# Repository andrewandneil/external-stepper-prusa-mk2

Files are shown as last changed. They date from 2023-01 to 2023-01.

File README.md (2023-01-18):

# External Stepper Drivers for Prusa MK2 Based Printers
Adds the ability to use external TMC stepper drivers on the Prusa MK2/S/2.5/S (any printer that uses the Mini Rambo).

## Purpose
Since the Mini Rambo that powers the original line of Prusas was released, stepper driver technology has come a long way. Now days, the `A4982`s that are hard soldered onto the board are louder and less accurate than more modern offerings from `Trinamic`.

The mission of this project is to create an open source PCB ~~and Case~~ design to allow the use of standard, off the shelf stepper driver boards to be used with printers such as the `Prusa MK2/S/2.5/S`. This will allow the printer to run quieter and smoother, resulting in a nicer experience whilst printing, as well as a nicer quality of print.

Achived by utilising the handily placed test points on the back of the Mini Rambo, this board is able to 'steal' the data signals intended for the `A4982`s on the board and give them to the user's choice of stepper drivers.

Side note: if you have a blown driver on your Mini Rambo, this is a great way of getting it up and running again. Simiply solder this board to the pads corresponding to the dead driver on the back of the board, and hey presto, a functional printer again!

Upon seeing a certain other design on the internet that did the same thing, but was closed source, I decided to create my own design from scratch, and make it open source! You will find all KiCAD PCB Design files, along with the F3D files and STEP files for the case I have created. 

## Functionality
Tested mostly with the `TMC2208` drivers, however, `TMC2209`s, `TMC2130`s and `TMC2100`s (may require to be in their 'standalone' mode) have all been tested and confirmed to work with this board and the printer. However, do note the graphic towards the bottom left of the PCB for the correct positioning of the jumpers for your stepper drivers.

Compatible with any printer using the Mini Rambo main board, including but not limited to `Prusa i3 MK2`, `Prusa i3 MK2S`, `Prusa i3 MK2.5` and `Prusa i3 MK2.5S`.

## Utilisation
This WILL require modifying your mainboard. However, the modification is not permant and can be reversed at any time. Only requires soldering to 8 fairly large points on the back of the main board. You will also need to get power for the board from somewhere. To do this you have 2 options:
  1. Tap into the 12V supplied from the printer's power supply and run a cable to the socket on the board.
  2. Run either a 12V or 24V external power supply and utilise that. 

The 24V option is your prefered option if you are wanting the drivers to operate as cool and quite as possible, however, please see the [optional](/Guides/PartsList.md/#optional) section of the parts list for more information.

#### Setting Stepper Current
My `TMC2208`s have been set to a Vref voltage of 1V[^1].

## What's Included?
In the repository you will find the KiCAD files if you wish to modify, adapt or improve the board ~~and a 3D printable case for the board, along with a STEP file if you wish to modify, adapat or improve it.~~ (yet to be added).

Please see the [releases](https://github.com/andrewandneil/external-stepper-prusa-mk2/releases) section to find the current Gerber files for the fabrication of the PCB.

## Software Used
  - [KiCAD](https://kicad.org): An amazing, open source, PCB design studio. I encourage you to check it out if you're looking for something like that. Used to design the schematics, PCB and export the Gerber Files.
  - [Fusion 360](https://www.autodesk.com/products/fusion-360): A good all round CAD software, with a free personal license. ~~Used to design the case.~~

## Pictures
To be added

## Cases

### My Case
As of the moment yet to be finalised

### Other People's Cases
In the offchance that someone either, modifies, redesigns, or creates from sctach a new case or related accessory, I'll do my best to add them here.

If you're one of amazing community that might create a case, get in touch with me and I'll link it here, along with any credit due.

## Parts List
Please see [here](/Guides/PartsList.md).

## Assembly Guide
Please see [here](/Guides/AssemblyGuide.md).

## What else
Notice how nowhere in this guide I mentioned the X and Y axis until now? Well, for good reason. If you wanted to you could build a board for the E and Z axis and use it in parallel to a X and Y board (or just use the E and Z board if you're weird like that I suppose). The Z motor plug will need to be split into 2 new plugs (one for ZL and ZR). The board labels the two sockets with X and Y identifiers, but this is more so you can trace which plug goes where. Obvisouly just connect either the X or Y plugs to the E or Z solder pads on the Rambo if you're planning on doing this.

However, logically with the X and Y axis doing the most moving and at the highest speeds, your best bet to make it mostly quiet is just making one for the X and Y.

## Future Plans
I have no clue if I will ever get around to implementing these plans but you might as well know about them (if I don't do them and you're reading this in the future please feel free to 'borrow' these ideas 😉):
  - Creating a board that allows X, Y, E and Z axis drivers all on one board.
  - Creating a 3D printable case for the board.
  - Test the board with even more drivers.
  - Create an easy to follow and detailed guide for assembly.

## Using these Files
This project is protected by a GNU GPL v3.0 license:
  - You are free to use the files and designs to create your own boards in a personal manner[^2].
  - You are also free to use the files and designs to create boards to sell and make a profit, so long as credit is given or a link is added to this GitHub page[^2].
  - You are also free to modify or otherwise change the files and designs included in anyway you see fit, so long as if the project is shared, it follows the GNU GPL v3.0 license and credit is given[^2].

I fully encourage you to do what you see fit with this design, so long as it follows the GNU license[^2]. If you have the know how and have an idea for an improvement, I look forward to see what you can do! After all, that's the spirit of RepRap!

[^2]:**Not legal adivce. Please read [COPYING.txt](/COPYING.txt) for the full GNU GPL v3.0 license**

## Currently Known Issues
##### Will do my best to update if other issues are found
  - Z and E motors will 'squeal' if using TMC drivers on X and Y axis. I believe this to be something to do with microstepping. Only happens if the motors are powered and at a certain rotational degree. *Your quick fix here is to ignore it or make a board for the E and Z axis*
    - It is completely unnoticable during motion. You will only really hear it if your printer is unlucky enough to stop in a rotaional positon where it happens.

## Disclamer
I have tested this board extensively and have yet to run into issues, however, if you choose to do this mod, you do so at your own risk. I, nor any other party involved, offer any kind of warranty with this product. I have done my best to include all relevant information in this GitHub page, to allow you to come to a decision as to wether or not you would like to partake in this mod. This is not a product. You must source and assemble the board yourself. I will do my best to support any issues you may have if I can.

[^1]: My reference voltage and therefore stepper current is just a suggestion not a defintive do it. Do your own research and experimentation to suit your steppers and drivers.

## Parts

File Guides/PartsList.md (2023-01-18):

# Parts You'll Need

### REQUIRED:
  - 1x printer with a functional Mini Rambo.
  - 1x PCB (find the gerber files for production [here](https://github.com/andrewandneil/external-stepper-prusa-mk2/releases/latest)).
  - 1x 2x8 2.54mm Pitch IDC cable.
  - 1x 2x8 2.54mm Pitch IDC PCB through-hole socket.
  - 2x stepper drivers (on breakout boards) of your choice ([see here for a list of working drivers](#your-stepper-driver-options)).
  - 2x Molex SL 1x4 2.54mm Pitch Male Vertical connectors.
    - [For example this from Digikey](https://www.digikey.co.uk/en/products/detail/molex/0705430003/114923).
    - Can be difficult to find these. You can of course suppliment them with standard 1x4 2.54mm pitch male headers if you wish.
  - 1x 2x3 2.54mm Pitch Male header.
  - 4x 1x8 2.54mm Pitch Female headers.
  - 2x 10K 0805 Resistors.
  - 1x wire-to-board terminal block, 5mm pitch with 2 terminals. (you could of course solder the power wires directly to the board if you'd like. Personally I would still use the terminals).
    - Something like:
      - [This from Farnell UK](https://uk.farnell.com/phoenix-contact/mkdsn-1-5-2-5-08-ht-bk/tb-wire-to-brd-2pos-16awg-blk/dp/3241413).
      - [This from Digikey](https://www.digikey.co.uk/en/products/detail/phoenix-contact/1729128/260615?productid=260615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).
      - Or [this on Amazon US](https://www.amazon.com/KeeYees-60pcs-Terminal-Connector-Arduino/dp/B07H5G7GC6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), only the 2 pin terminal type is required.
  - 2x 100uF 25V Radial capacitors, 6.3mm diameter and 2.50mm pitch.
    - Something like: 
      - [This from Farnell UK](https://uk.farnell.com/panasonic/eca1ehg101/cap-100-f-25v-20/dp/9692827).
      - Or [This from Digikey](https://www.digikey.co.uk/en/products/detail/rubycon/25ZL100MEFC6-3X11/3563144).

### Optional:
  - If you want to use an external power supply to power your drivers:
    - **DISCLAIMER: IF YOU CHOOSE THIS ROUTE YOU WILL BE MESSING WITH MAINS VOLTAGE. WETHER YOU BE IN A 110V or 240V COUNTRY THESE VOLTAGES CAN, AND WILL, KILL YOU IF NOT DONE PROPERLY. EITHER GET A QUALIFIED ELECTRICIAN TO HELP YOU OR JUST USE THE PRINTER'S SUPPLY!**
    - Honestly, here is where I am not going to help you with a specific part. 
    - You'll want either a 12V or 24V PSU (I recommend you just go for 24V if you're doing external anyway). 
    - You'll need to know how much current your steppers+drivers are going to use and do a simple `P=I*V` calculation to figure out your wattage. And remember to always OVER estimate your wattage and have headroom!!
    - **Please DO NOT buy a cheap Chinese PSU. Buy something decent if you're doing this, something like a Meanwell**.
  - If you wish to install a fan[^1][^2]:
    - 1x Pin Header, Square Pin, Signal, Wire-to-Board, 2.54 mm, 1 Rows, 3 Contacts, Through Hole Straight.
      - Something like:
        - [This from Farnell UK](https://uk.farnell.com/molex/22-27-2031/connector-header-3pos-1row-2-54mm/dp/9731156).
        - Or [This from Digikey](https://www.digikey.co.uk/en/products/detail/molex/0022232031/26669).
    - 1x Fan.
      - Something like a 40x10mm fan would do nicely for most drivers (a Noctua A4x10 ([Amazon US](https://www.amazon.com/Noctua-Cooling-Blades-Bearing-NF-A4x10/dp/B009NQLT0M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), [Amazon UK](https://www.amazon.co.uk/Noctua-NF-A4x10-Premium-Quiet-40x10mm/dp/B009NQLT0M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)) is perhaps your best option for 12V).

### Tools and Other:
  - Solder.
  - Soldering Iron.
  - Kapton Tape.
  - ~~If adding my 3D Printed case:~~ !(hasn't been finalised yet)!
    - ~~3D Printed case; [found here](https://www.printables.com/social/239130-utterotter/).~~
    - ~~x4 M3x10 Bolts.~~
    - ~~x4 M3 Nuts.~~
    - ~~x2 M3x18 Bolts.~~
  - Various HEX keys for disassembly of the printer.
  - Zip ties to replace cut zip ties during disassembly.
  - Some 20AWG or better guage wire for power delivery.
    - If you choose (and you should) to crimp the ends of these wires:
      - Crimper tool.
      - Crimps.

## Your Stepper Driver Options
Please note these are ones I have tested and worked with my Prusa i3 MK2.5S+.

This board can't magically add sensorless homing to your printer. Any driver that supports this mode will, and can work, but the endstop sensors of the printer are still required.

All drivers must be in their respective standalone modes (i.e. SPI/UART disabled). If you're not sure how to do that for your specific choice of driver Google is your friend.

Make sure your drivers have some form of heatsink included. If not I recommend you buy a fairly large heatsink for the driver.

### IMPORTANT: don't just buy the chip. You need the chip on a breakout board!
   - `Trinamic TMC2208`
     - Must have UART disbaled. (if you're not sure what that is or how to disbale it most `TMC2208` breakout boards have UART disabled by default).
     - One of the easiest and cheapest ways of getting quiet stepper drivers. 
     - Will run moderately hotter than the more modern `TMC2209`.
   - `Trinamic TMC2209`
     - Perhaps the best all round option.
     - Runs the quietest and coolest out of the four options listed here.
     - Sensorless homing does go to waste, along with other driver to board communication functions.
   - `Trinamic TMC2130`
     - Chris Riley has a great [YouTube video](https://www.youtube.com/watch?v=Jh8iwqc1TP0) on how to use the `TMC2130`s in standalone mode. Give it a watch
     - Runs in stealthChop or spreadCycle depending on jumper setup.
   - `Trinamic TMC2100`
     - Perhaps the least relevant option today.
     - Setup is very similar to `TMC2130`.
     - In my test it was the loudest of the four.
     - Runs in stealthChop or spreadCycle depending on jumper setup.

I am sure there are other drivers that are compatible with this setup. Please see [advanced tuning](/Guides/AdvancedTuning.md) if you wish to figure out if your chosen stepper driver is compatible.

[^1]: The fan will run at the voltage you are using for the power input into the board. So if you're running an external 12V power supply or tapping into the power from the printer you will need a 12V fan, or if you're using an external 24V power supply you will need a 24V fan.
[^2]: Fan is not strictly nessecary as if you have large enough heatsinks on your drivers, and don't run the motors at insane current levels, the drivers are perfectly capable of being passively cooled.

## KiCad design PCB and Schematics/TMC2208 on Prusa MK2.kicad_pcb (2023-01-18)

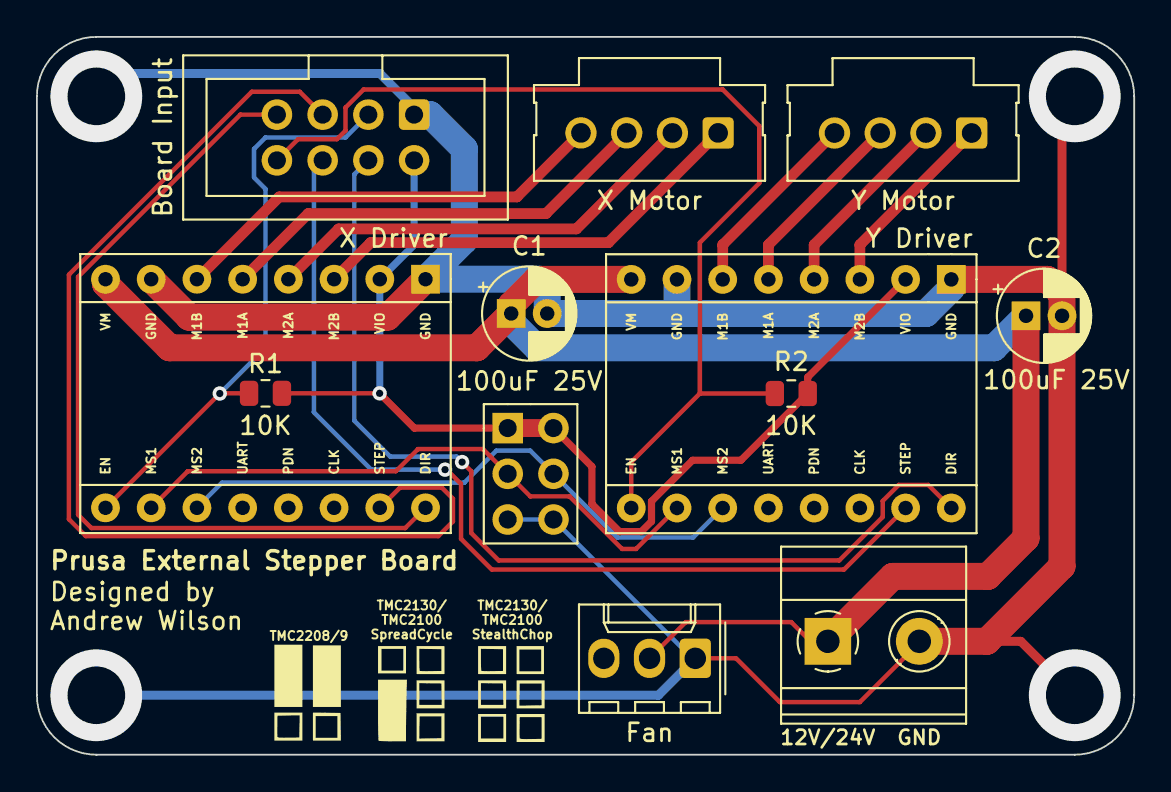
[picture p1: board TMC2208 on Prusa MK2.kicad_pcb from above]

Board: 2 copper layers, 61.0 x 39.9 mm, 12 parts (0 on the bottom side), 19 nets.

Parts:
Board Input: Conn_02x04_Odd_Even; IDC-Header_2x04_P2.54mm_Vertical
C1, C2: 100uF 25V; CP_Radial_D5.0mm_P2.00mm
Fan: Conn_01x03_Male; Molex_KK-254_AE-6410-03A_1x03_P2.54mm_Vertical
J1: Conn_02x03_Counter_Clockwise; PinHeader_2x03_P2.54mm_Vertical
J4: Screw_Terminal_01x02; TerminalBlock_Phoenix_MKDS-1,5-2-5.08_1x02_P5.08mm_Horizont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
R1, R2: 10K; R_0805_2012Metric
X Motor: Conn_01x04_Male; Molex_SL_171971-0004_1x04_P2.54mm_Vertical
XDriver1: Trinamic_Breakout_TMC2208; Trinamic_Breakout-16_15.2x20.3mm
Y Motor: Conn_01x04_Male; Molex_SL_171971-0004_1x04_P2.54mm_Vertical
YDriver1: Trinamic_Breakout_TMC2208; Trinamic_Breakout-16_15.2x20.3mm

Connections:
+12V: C1.1, C2.1, Fan.2, J4.1, XDriver1.8 (VM), YDriver1.8 (VM)
/CONFIG1: J1.3, XDriver1.10 (MS1), YDriver1.10 (MS1)
/CONFIG2: J1.4, XDriver1.11 (MS2), YDriver1.11 (MS2)
GND: Board Input.1, C1.2, C2.2, Fan.1, J1.5, J1.6, J4.2, XDriver1.1 (GND), XDriver1.7 (GND), YDriver1.1 (GND), YDriver1.7 (GND)
unnamed: Board Input.3, R1.1, XDriver1.9 (~ENABLE)
unnamed: Board Input.4, YDriver1.16 (DIR)
unnamed: Board Input.5, XDriver1.15 (STEP)
unnamed: Board Input.6, YDriver1.15 (STEP)
unnamed: Board Input.7, XDriver1.16 (DIR)
unnamed: Board Input.8, R2.2, YDriver1.9 (~ENABLE)
unnamed: X Motor.1, XDriver1.3 (M2B)
unnamed: X Motor.2, XDriver1.4 (M2A)
unnamed: X Motor.3, XDriver1.5 (M1A)
unnamed: X Motor.4, XDriver1.6 (M1B)
unnamed: Y Motor.1, YDriver1.3 (M2B)
unnamed: Y Motor.2, YDriver1.4 (M2A)
unnamed: Y Motor.3, YDriver1.5 (M1A)
unnamed: Y Motor.4, YDriver1.6 (M1B)
VCC: Board Input.2, J1.1, J1.2, R1.2, R2.1, XDriver1.2 (VIO), YDriver1.2 (VIO)

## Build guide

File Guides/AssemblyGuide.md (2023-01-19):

# Assembly Guide

## Step 1
As with any guide you will need to check you have all the required [parts](/Guides/PartsList.md).
Here is a quick overview to double check you have everything for the PCB side:
  - 1x PCB
  - 1x IDC Connector
  - 2x 0805 Resistors
  - 2x Capacitors
  - 1x Terminal Block
  - 1x 2x3 Male Pin Headers

Optionally:
  - 1x Fan Header
  - 4x Female Pin Headers



## Step 2
Now you'll need to solder everything to the board. I'm not going to baby step you through this step, as you should already know how to do this.

A general rule of thumb for soldering components to a PCB is to start with the shortest components first and work your way up.

Here you can also choose to add the 1x8 female pin headers or just solder the chips directly to the board. (I recommend using the pin headers).



You will also need to set your jumper configurations now. If you look at the bottom left of the PCB (also shown in image below) you should see a diagram for how you will need to do it. Make sure you configure these correctly for your driver! Incorrect configuration will likely cause wildly incorrect axis movements.

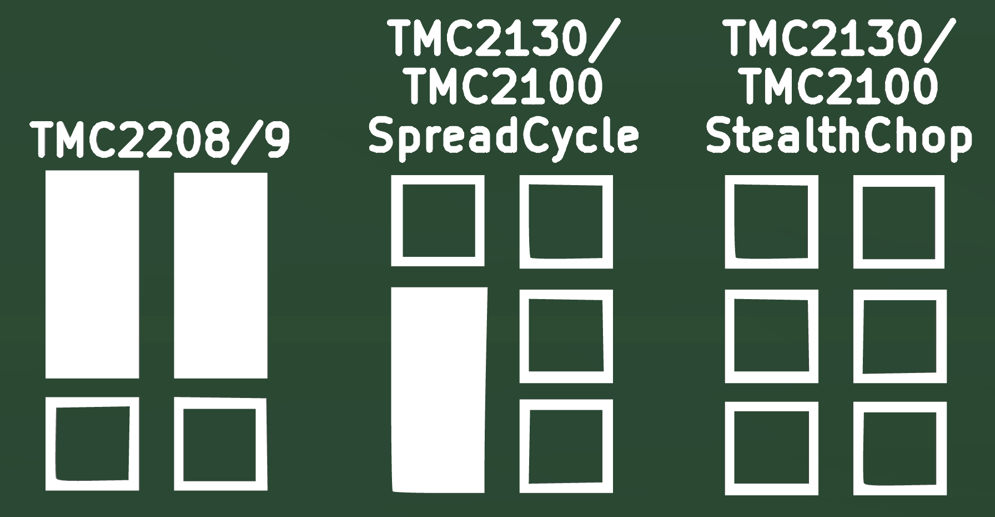
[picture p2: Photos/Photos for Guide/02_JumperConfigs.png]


Make sure your jumpers are configured for your chips as below:

**`TMC2208` or `TMC2209`:**



**`TMC2130` or `TMC2100` spreadCycle:**



**`TMC2130` or `TMC2100` stealthChop:**



## Step 3
Now you need to take your 8 pin IDC cable and cut off one end. Hopefully, you'll have a cable where the 2 ends point different directions. You'll most likely want the direction that allows the cable to come directly away from your PCB rather than needing to over it:




## Step 4

## Step 5
**This step is very important! Pay close attention and double check what you're doing or it could result in damage to either your Mini Rambo or stepper drivers!**

Now you need to take your IDC cable and solder it to the points shown below. If I were you I would cut the individual cables to length as you go to get a nice clean and uniform look. See the image in [Step 6](#step-6) for a better look.

**YOU MUST DOUBLE CHECK THAT YOU HAVE THE CORRECT PIN ON RAMBO TO THE CORRECT PIN ON THE PCB**
  * You can check this by using a multimeter and ensuring that the label on the back of the PCB corresonds to the correct test point on the back of the Mini Rambo.
  * The labels for the pins can be found on the back of the PCB next to the corresponding pin on the IDC connector.

###### If you're doing this mod for the Z and E axis it goes without saying that you should replace X and Y with E and Z.

| Test Point Label on the Mini Rambo | Corresponding Label on PCB |
|---|---|
| XDIR | XDIR |
| XSTEP | XS |
| XEN | XEN |
| YDIR | YDIR |
| YSTEP | YS |
| YEN | YEN |




## Step 6
Last two points to solder to the Rambo is the GND and VCC Pins.

These two points are rather simple and just need to be soldered as below.



With that all completed the back of your Mini Rambo should look something like this:


## Step 7
Nice! You've finished the hard part! Give yourself a pat on the back. Now we need to do the fun bit, wiring!

This is where the guide will split into two for a bit, [Step 7-1](#step-7-1) is for the people using the printer's power supply and [Step 7-2](#step-7-2) is for those of you using external power supplies.

### Step 7-1
#### For people using the printer's power supply

You will now need to tap into the 12V power rails for the Mini Rambo. As a general rule use the `PWR IN` power lines and not the `BED IN` power lines to avoid potential issues.

There are multiple ways of doing this: 
  - You can solder the wires directly to the back of the `PWR IN` terminal on the back of the Mini Rambo. 
    - I wouldn't recommend this as it's more difficult and you're more likely to damage somehting in the process.
  - You can add additonal wires to the crimp connector on the Mini Rambo side of the power supply.
    - This is the option I choose as it required the least wire and least disassembly.
  - Or you can tap into the terminals on the printer's power supply, i.e. direct from the source.
    - **THIS METHOD REQUIRES MESSING WITH AN AREA DESINGED FOR MAINS VOLTAGE. WETHER YOU BE IN A 110V or 240V COUNTRY THESE VOLTAGES CAN, AND WILL, KILL YOU IF NOT DONE PROPERLY. EVEN IF THE POWER CABLE IS REMOVED THE CAPACITORS CAN STILL HOLD A DEADLY CHARGE. EITHER GET A QUALIFIED ELECTRICIAN TO HELP YOU OR CHOOSE ONE OF THE OTHER TWO OPTIONS**
    - With that being said, it's perhaps one of most secure options, however, requires disassembly of the printer's power supply shroud.

Whichever option you choose, it's always a good idea to check for shorts before continuing.

What I did was take my wires and wrap them around the wires already inside the crimp terminals on the Rambo. I then placed the crimp+wire combination back inside the terminal and clamped it down. I know it doesn't sound the best but nothing has gone wrong yet and the connection is very solid.

I am sure if you've gotten this far in the mod you know what you're doing at least somewhat. Make your own decisions with the information provided.

What my connector looks like:


Now go onto [Step 8](#step-8).

### Step 7-2
#### For people using an external 12V or 24V power supply
**I WOULD LIKE TO STESS AGAIN THAT IF YOU CHOOSE THIS ROUTE YOU WILL BE MESSING WITH MAINS VOLTAGE. WHETHER YOU BE IN A 110V or 240V COUNTRY THESE VOLTAGES CAN, AND WILL, KILL YOU IF NOT DONE PROPERLY. EITHER GET A QUALIFIED ELECTRICIAN TO HELP YOU OR JUST USE THE PRINTER'S SUPPLY!**

(I know, I know, this is the 3rd time I've mentioned it, but trust me I know from experience you do not want 240V coursing through your veins! ☺️)

This step depends heavily on your choice of power supply. However, it is likely that:
  - You will need to wire Live, Neutral and Earth to their respective terminals.
  - You will need a wire from GND on the PSU to the `-` on the PCB.
  - You will need a wire from 12/24V on the PSU to the `+` on the PCB.
  - You will need to ensure that if your PSU comes with a voltage switch that you set it to your local voltage.
  - And I **STRONGLY** recommend some form of 3D printed cover to go over the terminals when you're done. Exposed mains voltage is no joke.

Also, do not connect the external PSU to the Rambo in any way! Only connect it to the `+` and `-` on the breakout board.

Now go onto [Step 8](#step-8).

## Step 8
Now it's time for reassembly. 

>__Warning__
>
>I strongly recommend you double check you have wired everything correctly between the Mini Rambo and the breakout board using a multimeter, whilst you still have it out the case.
>
>Check the polarity one last time (as shown in [Step 5](#step-5)). Once you've confirmed everything is good, you can continue.

Take your Mini Rambo and place it back into the Mini Rambo's housing. Place the housing back onto the printer and plug all the wires back in. However, leave the X and Y (or the E and Z, depending) stepper motor cables unplugged from the Mini Rambo. We will need to plug these into your breakout board in order for the drivers to, well, drive them.



## Step 9
Now you're going to want to plug all the connectors into the board.

You may already know where everything goes but here's a reminder:
  1. `Board Input` IDC Connector. This is where you plug in the IDC cable that you soldered to the back of the Mini Rambo
  2. `X Motor` Molex SL. This is where the plug for the X axis stepper goes into.
  3. `Y Motor` Molex SL. This is where the plug for the Y axis stepper goes into.
  4. `X Driver` x2 1x8 Female Headers. This is where you plug in the stepper driver for your X axis.
  5. `Y Driver` x2 1x8 Female Headers. This is where you plug in the stepper driver for your Y axis.
  6. 2x3 Male Header. This is where you will need to set your jumper configurations. See [Step 2](#step-2) if you havent configured them already.
  7. `Fan` 1x3 (if installed). This is where you can optionally plug in a fan.
  8. `12/24V GND` 2 port Terminal. This is where you should have placed your power wires from [Step 9](#step-9). If you're using my case you will need to remove them for the next step.



## Step 10

### This part of the guide is written for my version of the case. Suppliment this step if using a 3rd party case, your own design, or no case at all.
It's time for a case. 

If using my case make sure you have on hand:
  - 1x Case.
  - 2x Arm Pieces.
  - 4x M3x10 Bolts. (2 of these bolts can be salvaged from the Mini Rambo's mounts as we replace them with longer bolts)
  - 4x M3 Nuts.
  - 2x M3x?? Bolts.

##### Please note this case is likely to change as I improve the design. The concept should remain the same, but do not be alarmed if your case looks different to the one in the photos

  1. Take the two 'arm' pieces of the case and push fit them into the part designed to house the board.


  2. Now install the breakout board into the case (note: you may need to remove the power cables temporarily from the board if installed. Place them back in when the PCB is inside the case).


  3. Place the 4 M3 nuts into the hexagon shapped holes on the back of the case.


  4. Now install the 4 M3x10 screws, and tighten them into the nuts.


  5. Take the bottom two screws and nuts out of the Rambo (if not done already) and push the hexagon protrusions into the cavity left by removing the nuts.



  6. Add the removed nuts to the holes behind the protrusions.


  7. Now simiply add your M3x?? screws through the Mini Rambo into the installed nuts.


Congratulations you now have the case installed.

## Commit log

2023-01-18 Added a required part to be a PCB
2023-01-18 Added PCB and Schematics
    [TMC2208 on Prusa MK2.kicad_pcb, TMC2208 on Prusa MK2.kicad_sch]
